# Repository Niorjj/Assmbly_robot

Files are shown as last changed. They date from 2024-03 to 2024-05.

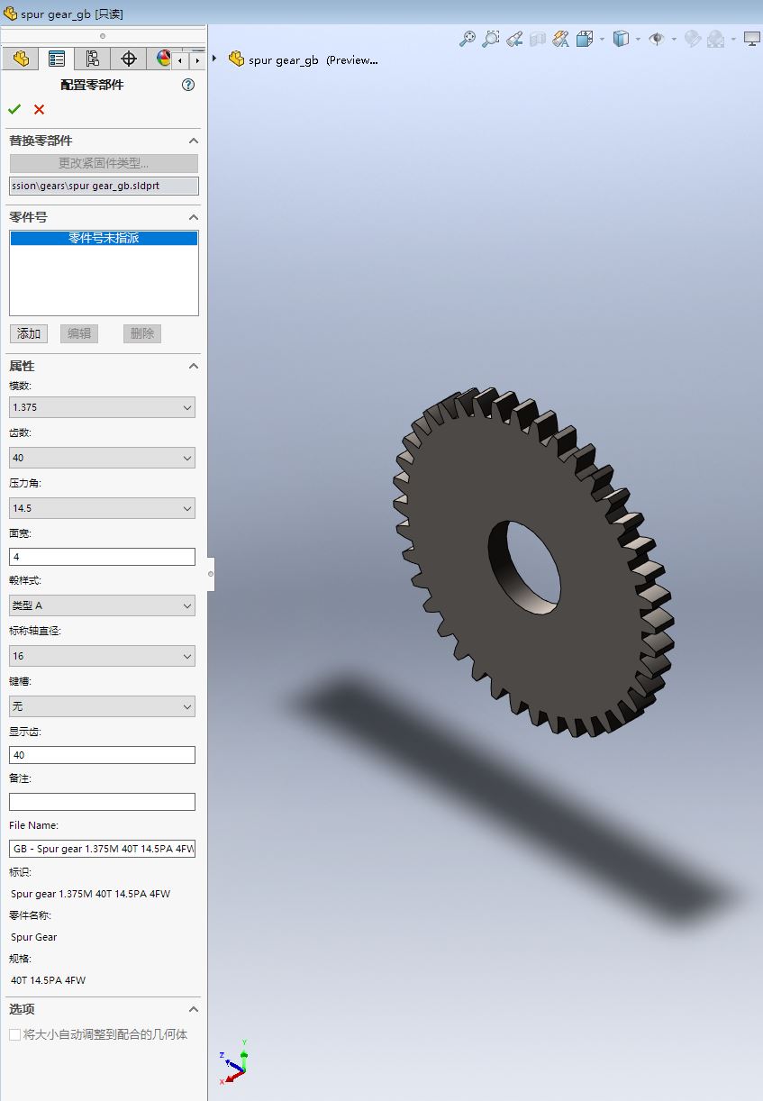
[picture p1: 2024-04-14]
Assembly_robot/hardware/MachineConstruction_project/solidworks/齿轮1_1.JPG

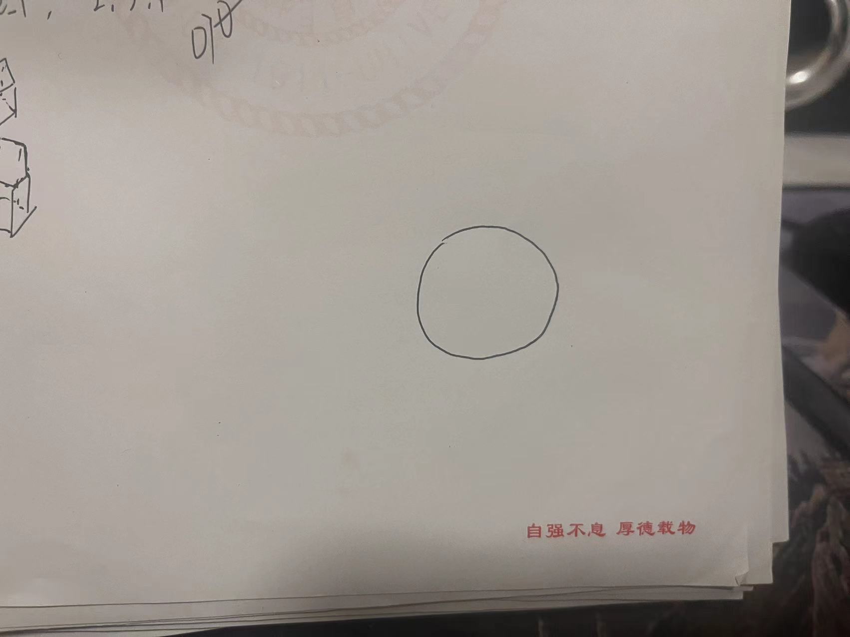
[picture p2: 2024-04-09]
Assembly_robot/software/Python_Code/test_circle.jpg

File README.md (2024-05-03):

<<<<<<< HEAD
## 项目简介

### 规则
=======
# Assembly_robot

### 项目简介

#### 规则
1. 传送带控制
**只需控制启动和停止，高电平启动，低电平停止**
2. 提供标准 220V 电源接口
**现场提供电源**
3. 待装配体旋转平台控制
**待装配体旋转平台接入PUL，DIR，EN三种信号**
4. 初始最大闭合区域
**450mm*450mm**
5. 布线层印有学校名称和2023，提供完整原理图和PCB图
6. 提供全套总装图和零件加工图

### 结构划分
=======

#### 项目流程图
1. 软件部分
   1. 树莓派相机标定
   2. 颜色与形状识别
   3. 串口通信将各电机转动角度发送到stm32上
   4. stm32驱动各电机转动
   5. 控制圆台和传送带
2. 外设资源分配
3. 原理图及pcb
4. 机械结构
5. 调试

#### 相机识别步骤
1. 相机标定
    相机标定的合格指标一共有四个，分别是*x轴方向*、*y轴方向*、*远近*以及*旋转角度*。
2. 相机和机械臂进行手眼标定
3. 读取摄像头信息
4. 识别出目标物体并得出位姿
5. 物体在相机中的二维坐标转化成相对于相机光心的三维坐标
6. 再转换成相对于机械臂底座的世界坐标
7. 计算机械臂末端执行器抓取物体时的位姿
8. 通过已知的目标位置和末端执行器的位姿信息来计算机械臂上每个电机应转动的角度
9.  根据有无障碍物、路径距离要求、时间要求规划出合适的路径
10. 驱动机械臂各个关节一步一步到达合适的位置
11. 末端执行器抓取物体
12. 投放到指定位置

#### 主要参数
1. **x**相机标定位置x坐标
2. **y**相机标定位置y坐标
3. **h**相机标定位置与相机距离
4. **r**相机标定识别物体旋转角度
5. **j1_Angle**大臂电机转动角度
6. **j2_Angle**小臂电机转动角度
7. **j3_Angle**底部电机转动角度
8. **j4_Angle**直线模组电机转动角度
9. **j5_Angle**机械爪夹取电机转动角度
10. **j6_Angle**舵机旋转角度
11. **PLANT_Angle**圆盘转动角度
12. **TRANS_State**传送带启停状态

#### 机械臂逆运动学求解
1. 确定目标位置
2. 求解各电机转动的角度python(Inverse_Kinematics)
3. Matlab Robotic System toolbox

#### 目前主要需要攻克的问题
1. 充分利用现有材料
2. 主控板用最小系统板，驱动板自制PCB
3. 直线模组的长度
4. 3D打印材料，受力情况
5. 模型尽量更改为用亚克力板，3D打印材料，铝型材组合的
6. 模型逆运动学，相机位置

后续正在补充ing....

<<<<<<< HEAD
### 
=======
####

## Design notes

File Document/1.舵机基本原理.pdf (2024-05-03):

# 舵机基本原理

最近几年国内机器人开始起步发展，很多高校、中小学都开始进行机器人技

术教学。小型的机器人、模块化的机器人、组件式的机器人是教学机器人的首选。

在这些机器人产品中，舵机是很关键，使用较多的部件。根据控制方式，舵机应

该称为微型伺服马达。早期在模型上使用最多，主要用于控制模型的舵面，所以

俗称舵机。舵机接受一个简单的控制指令就可以自动转动到一个比较精确的角

度，所以非常适合在关节型机器人产品使用。

## 1.舵机的结构

舵机简单的说就是集成了直流电机、电机控制器和减速器等，并封装在一个

便于安装的外壳里的伺服单元。能够利用简单的输入信号比较精确的转动给定角

度的电机系统。舵机安装了一个电位器（或其它角度传感器）检测输出轴转动角

度，控制板根据电位器的信息能比较精确的控制和保持输出轴的角度。这样的直

流电机控制方式叫闭环控制，所以舵机更准确的说是伺服马达，英文 servo。

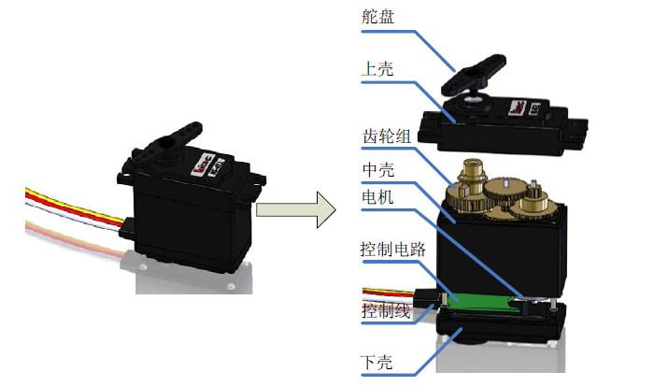
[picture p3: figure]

图 1 舵机的结构

舵机的主体结构如图 1 所示，主要有几个部分：外壳、减速齿轮组、电机、

电位器、控制电路。简单的工作原理是控制电路接收信号源的控制信号，并驱动

电机转动；齿轮组将电机的速度成大倍数缩小，并将电机的输出扭矩放大响应倍

数，然后输出；电位器和齿轮组的末级一起转动，测量舵机轴转动角度；电路板

检测并根据电位器判断舵机转动角度，然后控制舵机转动到目标角度或保持在目

标角度。

舵机的外壳一般是塑料的，特殊的舵机可能会有金属铝合金外壳。金属外壳

能够提供更好的散热，可以让舵机里面的电机运行在更高功率下，以提供更高的

扭矩输出。金属外壳也可以提供更牢固的固定位置。舵机的齿轮箱有塑料齿轮、

混合齿轮、金属齿轮的差别。塑料齿轮成本底，噪音小，但强度较低；金属齿轮

强度高，但成本高，在装配精度一般的情况下会有很大的噪音。小扭矩舵机、微

舵、扭矩大但功率密度小的舵机一般都用塑料齿轮，如 Futaba 3003，辉盛的 9g

微舵。金属齿轮一般用于功率密度较高的舵机上，比如辉盛的 MG995 舵机，在和

3003 一样体积的情况下却能提供 13KG 的扭矩。Hitec 甚至用钛合金作为齿轮材

料，其高强度能保证 3003 大小的舵机能提供 20 几公斤的扭矩。混合齿轮在金属

齿轮和塑料齿轮间做了折中，在电机输出减速箱扭矩不大的部位，用塑料齿轮。

## 2.舵机的规格和选型

2.1 舵机转速

转速由舵机无负载的情况下转过 60°角所需时间来衡量，常见舵机的速度

一般在 0.11s/60°-0.21s/60°之间。

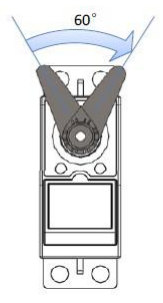
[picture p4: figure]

图 2 舵机的转速
2.2 舵机转矩

舵机扭矩的单位是 KG·CM，这是一个扭矩单位。可以理解为在舵盘上距舵

机轴中心水平距离 1CM 处，舵机能够带动的物体重量。

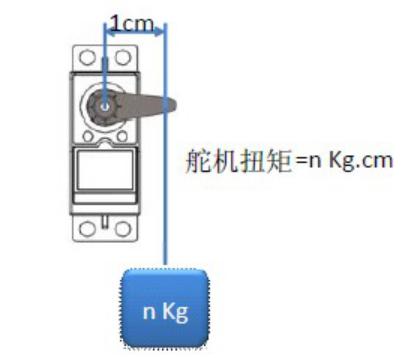
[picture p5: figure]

图 3 舵机的转矩

2.3 工作电压

厂商提供的速度、转矩数据和测试电压有关，在 4.8V 和 6V 两种测试电压下

这两个参数有比较大的差别。如 MG995 在 4.8V 时速度为 0.17 秒，在 6.0V 时

速度为 0.13 秒。舵机的工作电压对性能有重大的影响，舵机推荐的电压一般都

是 4.8V 或 6V。当然，有的舵机可以在 7V 以上工作，比如 12V 的舵机也不少。

具体更加较高的电压可以提高电机的速度和扭矩。选择舵机还需要看我们的控制

板所能提供的电压。

2.4 尺寸、重量和材质

舵机的功率（速度×转矩）和舵机的尺寸比值可以理解为该舵机的功率密度，

一般同样品牌的舵机，功率密度大的价格高。塑料齿轮的舵机在超出极限负荷的

条件下使用可能会崩齿，金属齿轮的舵机则可能会电机过热损毁或外壳变形。所

以材质的选择并没有绝对的倾向，关键是将舵机使用在设计规格之内。用户一般

都对金属制的物品比较信赖，齿轮箱期望选择全金属的，舵盘期望选择金属舵盘。

但需要注意的是，金属齿轮箱在长时间过载下也不会损毁，最后却是电机过热损

坏或外壳变形，而这样的损坏是致命的，不可修复的。塑料出轴的舵机如果使用

金属舵盘是很危险的，舵盘和舵机轴在相互扭转过程中，金属舵盘不会磨损，舵

机轴会在一段时间后变得光秃，导致舵机完全不能使用。综上，选择舵机需要在

计算自己所需扭矩和速度，并确定使用电压的条件下，选择有 150%左右甚至更

大扭矩富余的舵机。

## 3.舵机的工作原理

舵机是一个微型的伺服控制系统，具体的控制原理可以用下图表示：

工作原理是控制电路接收信号源的控制脉冲，并驱动电机转动；齿轮组将电

机的速度成大倍数缩小，并将电机的输出扭矩放大响应倍数，然后输出；电位器

和齿轮组的末级一起转动，测量舵机轴转动角度；电路板检测并根据电位器判断

舵机转动角度，然后控制舵机转动到目标角度或保持在目标角度。模拟舵机需要

一个外部控制器（遥控器的接收机或者单片机）产生脉宽调制信号来告诉舵机转

动角度，脉冲宽度是舵机控制器所需的编码信息。舵机的控制脉冲周期 20ms，

脉宽从 0.5ms-2.5ms，分别对应-90 度到+90 度的位置(对于 180°舵机)。如下图

所示：

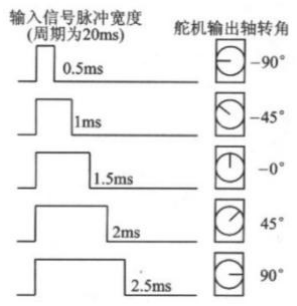
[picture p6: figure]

需要解释的是舵机原来主要用在飞机、汽车、船只模型上，作为方向舵的调

节和控制装置。所以，一般的转动范围是 45°、60°或者 90°，这时候脉冲宽

度一般只有 1ms-2ms 之间。而后舵机开始在机器人上得到大幅度的运用，转动的

角度也在根据机器人关节的需要增加到-90°至 90°之间,甚至还有-135°至

135°之间，脉冲宽度也随之有了变化。对与机器人控制而言，我们一般通过单

片机产生 PWM 信号控制舵机。

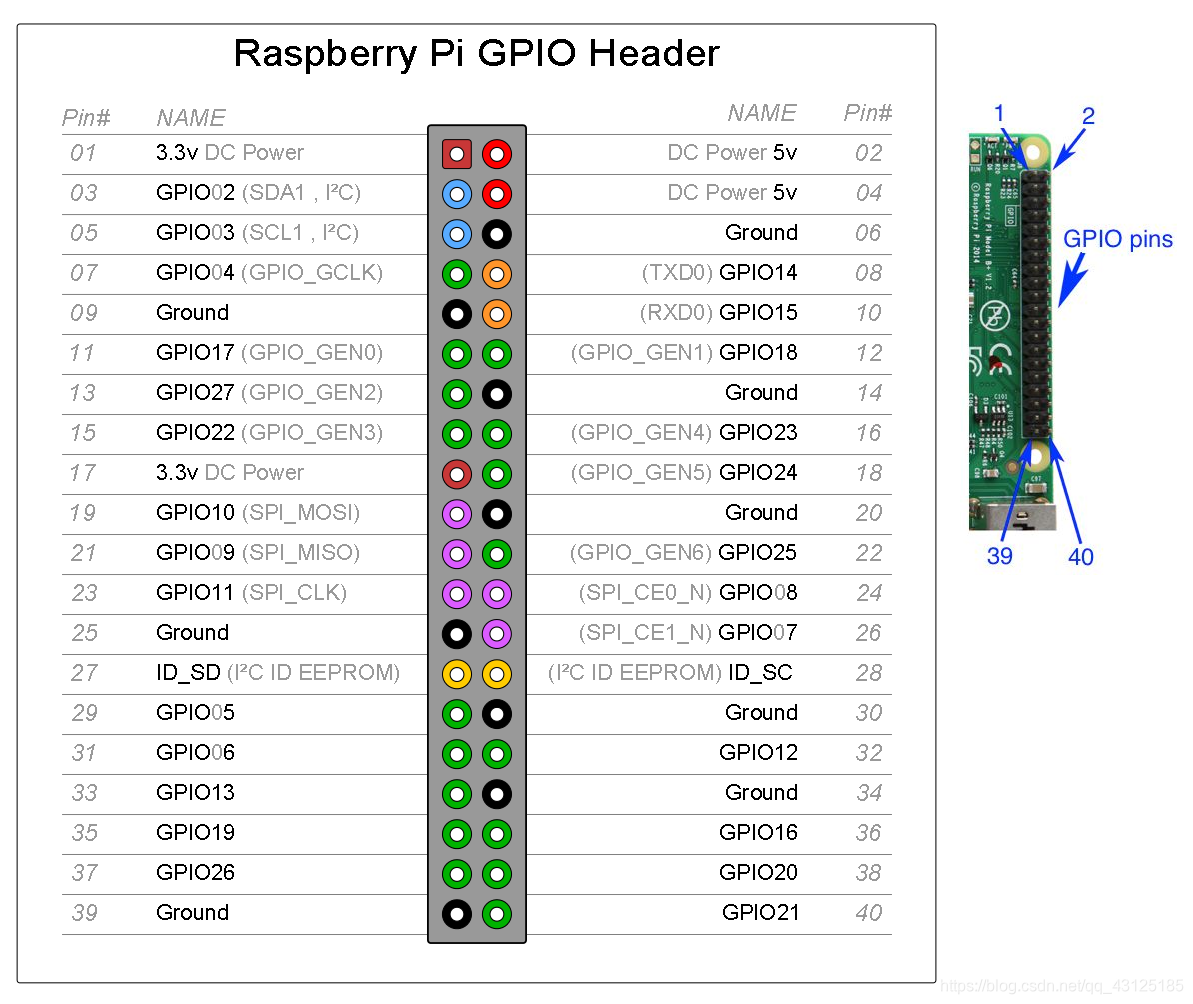
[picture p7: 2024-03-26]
Document/树莓派引脚图.jpg

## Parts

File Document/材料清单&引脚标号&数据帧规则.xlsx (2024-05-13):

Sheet: 材料表
结构分类 | 名称 | 型号 | 数量 | 单价 | 总价 | 备注
核心处理器 | 树莓派 |  | 1
 | 摄像头 |  | 1
控制器 | stm32f103RCT6最小系统板带屏幕 |  | 1 | 49.9 | 49.9
 | 驱动板 |  | 1 | 71.88 | 71.88 | PCB板20元，元器件51.88元
机械结构 | 步进电机 |  | 5 |  |  | 直线模组*1 底部旋转*1 大臂角和小臂角*2 机械爪抓取*1
 | 舵机 |  | 1
 | 联轴器
 | 直线丝杠装置 |  | 1
 | 外壳 |  |  |  |  | 3D打印制作，亚克力板，铝型材
 | 电源适配器 |  | 1 |  |  | 220V转12V
 | 传动齿轮
 | xh2.54-4p转母线 |  | 1 |  |  | 核心板串口连接树莓派
 | xh2.54-6p转公线 |  | 2 |  |  | 电机驱动板连接核心板

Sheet: 引脚
STM32F103RCT6 | 引脚名 | 功能 | 描述 | 树莓派 | 功能 | 功能 |  | 驱动板 |  | 电机 | 描述 | 传送带/装配圆盘
 | PA8 | TIM1_CH1 | 大臂舵机 |  |  |  | 接线端子 |  |  | SERVO1 | 大臂舵机
 | PA11 | TIM1_CH4 | 小臂舵机 |  |  |  |  |  |  | SERVO2 | 小臂舵机
 | PA1 | TIM2_CH2 | 底部旋转舵机 |  |  |  |  |  |  | SERVO3 | 底部旋转舵机
 | PA2 | TIM2_CH3 | 机械爪夹取舵机 |  |  |  |  |  |  | SERVO4 | 夹取舵机
 | PA3 | TIM2_CH4 | 机械爪旋转舵机 |  |  |  |  |  |  | SERVO5 | 旋转舵机
 | PC7 | TARANS | 传送带启停端 |  |  |  |  |  |  |  |  | D+ | 连接传送带启停端
 | PA1 | PLANT_DIR | 装配圆盘DIR |  |  |  |  |  |  |  |  | DIR
 | PC15 | PLANT_EN | 装配圆盘EN |  |  |  |  |  |  |  |  | EN
 | PB3 | MOTOR1_PUL | 底部步进电机PUL
 | PB4 | MOTOR1_DIR | 底部步进电机DIR
 | PB5 | MOTOR1_EN | 底部步进电机EN
 | PC10 | USART4_TX | 串口1输出 | GPIO15 | RX | 串口1输入
 | PC11 | USART4_RX | 串口1输入 | GPIO14 | TX | 串口1输出
 | PA13 | SWDIO | 调试数据段
 | PA14 | SWCLK | 调试时钟端
 | PD0 | HSE_IN
 | PD1 | HSE_OUT |  | 3.3V | 高电平点
 | VDD |  | 高电平点 | GND | 低电平点 |  |  | VCC | 连接5V
 | VSS |  | 低电平点 |  |  |  |  | GND
 | VBAT |  | 电池引脚 |  |  |  |  | VM | 连接12V
 | NRST |  | 复位引脚
 | PB2 | BOOT0 | 启动 |  |  |  |  | STBY | 连接5V
 |  | BOOT1

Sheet: 数据帧规则
数据位 | 数据 | 功能
Byte0 | 0xAA | 起始字节1
Byte1 | 0xBB | 起始字节2
Byte2 | J1_Angle | 大臂角度
Byte3 | J2_Angle | 小臂角度
Byte4 | J3_Angle | 底部旋转电机角度
Byte5 | J4_Angle | 底部平移电机角度
Byte6 | J5_ | 夹取舵机角度
Byte7 | J6_Angle | 旋转舵机角度
Byte8 | PLANT_Angle | 圆盘转动角度
Byte9 | TRANS_State | 传送带启停状态
Byte10 | 0xFF | 结束位
Bode_rate | 115200

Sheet: 角度对应规则
 | 500 | 800 | 1000 | 1450 | 1500 | 2000 | 2100
大臂舵机
小臂舵机
底部旋转舵机 |  | -90 |  | 0 |  |  | 90
机械爪夹取舵机 |  |  | 张开 |  | 张开 | 闭合
机械爪旋转舵机 | -45 |  | 0 |  | 45 | 90
 |  |  |  |  |  |  |  | s

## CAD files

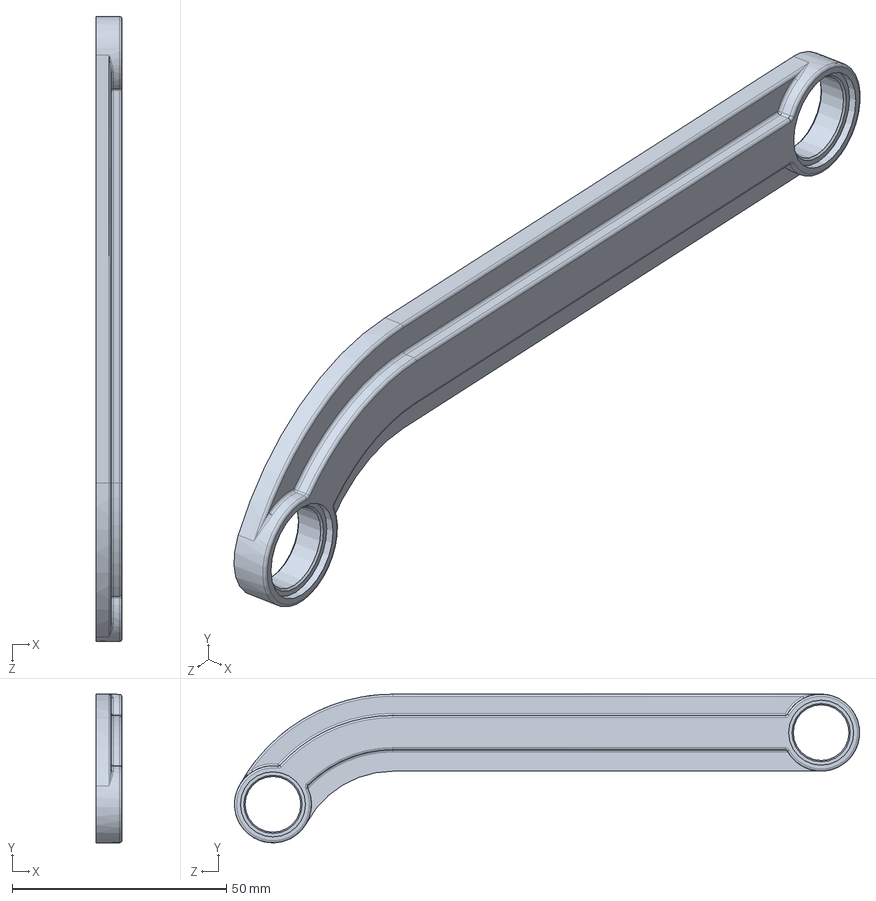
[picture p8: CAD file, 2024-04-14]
Assembly_robot/hardware/MachineConstruction_project/solidworks/零件6（2）.SLDPRT
6.00 x 34.7 x 145.9 mm

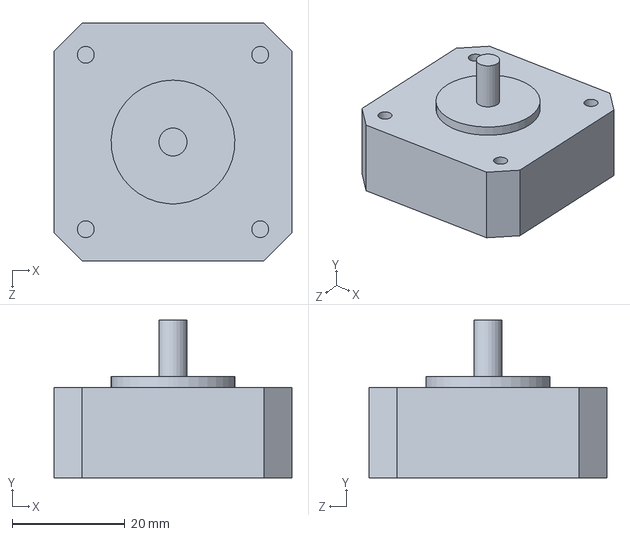
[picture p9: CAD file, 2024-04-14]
Assembly_robot/hardware/MachineConstruction_project/solidworks/电机2.SLDPRT
42.3 x 28.0 x 42.3 mm

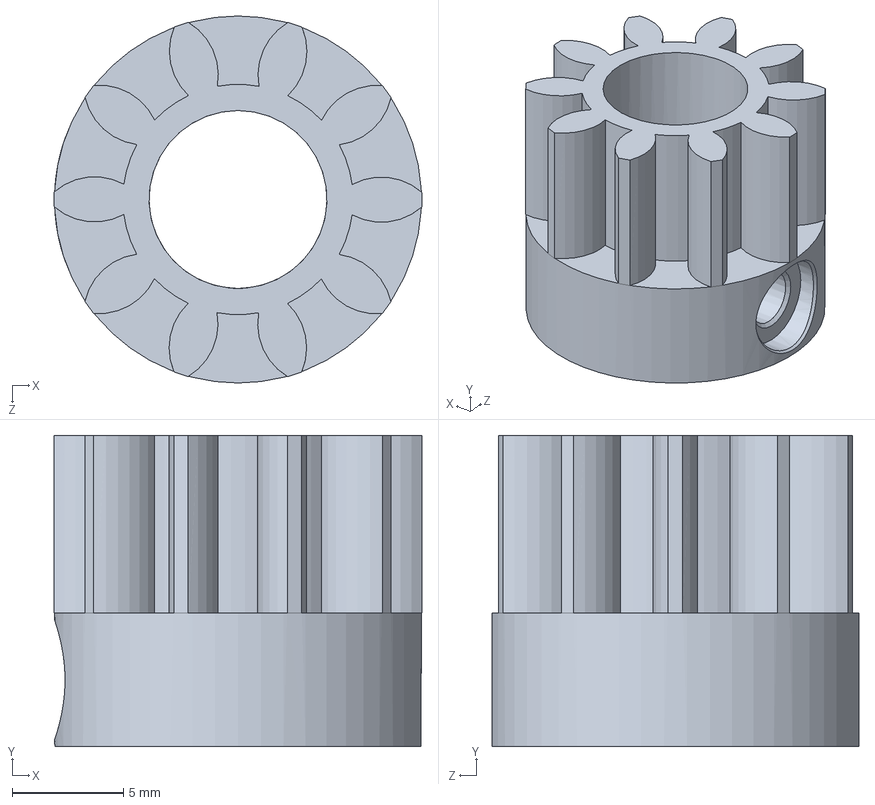
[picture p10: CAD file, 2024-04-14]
Assembly_robot/hardware/MachineConstruction_project/solidworks/齿轮3.1.SLDPRT
16.5 x 14.0 x 16.5 mm

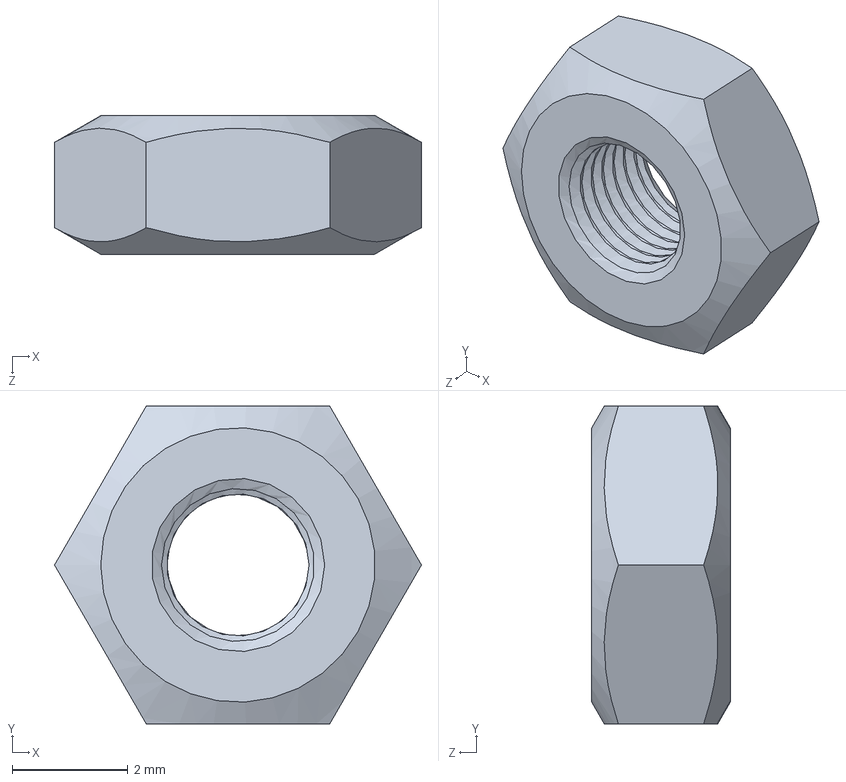
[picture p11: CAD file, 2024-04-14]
Assembly_robot/hardware/MachineConstruction_project/solidworks/M3-S_1.SLDPRT
6.35 x 5.50 x 2.40 mm

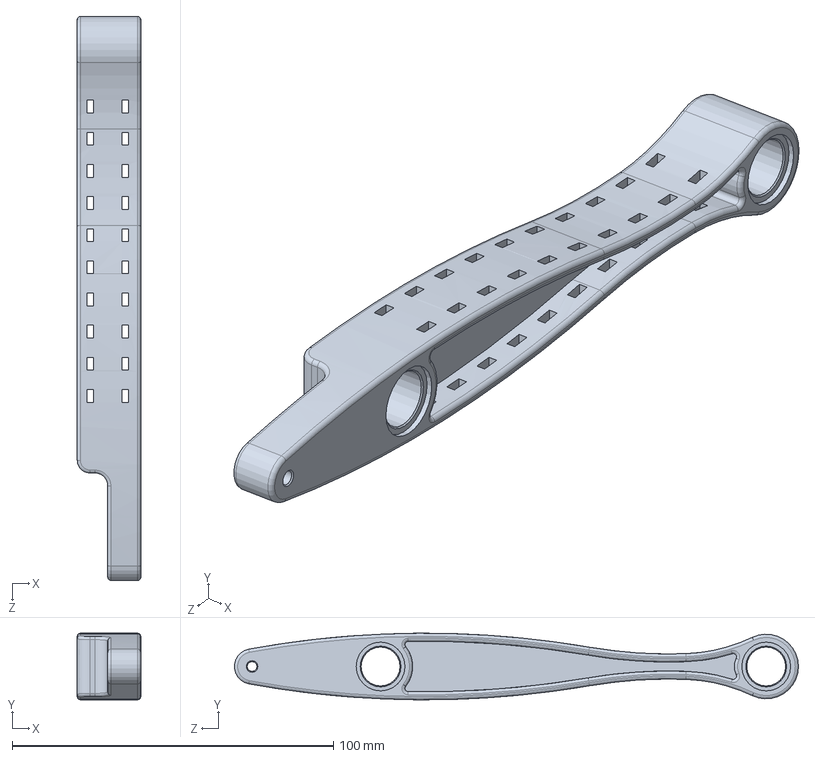
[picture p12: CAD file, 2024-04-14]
Assembly_robot/hardware/MachineConstruction_project/solidworks/零件4.SLDPRT
19.8 x 20.7 x 175.5 mm

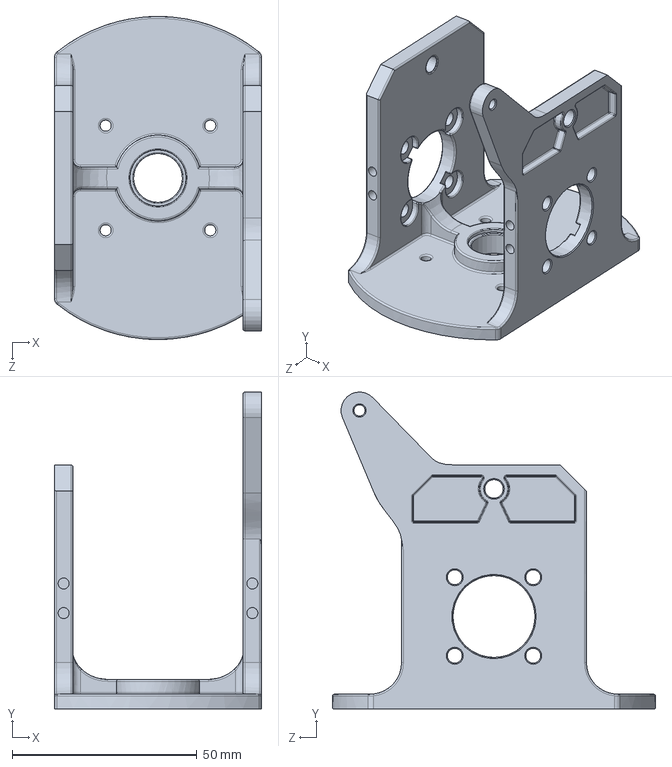
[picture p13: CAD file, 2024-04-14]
Assembly_robot/hardware/MachineConstruction_project/solidworks/零件1.SLDPRT
56.0 x 85.7 x 87.3 mm

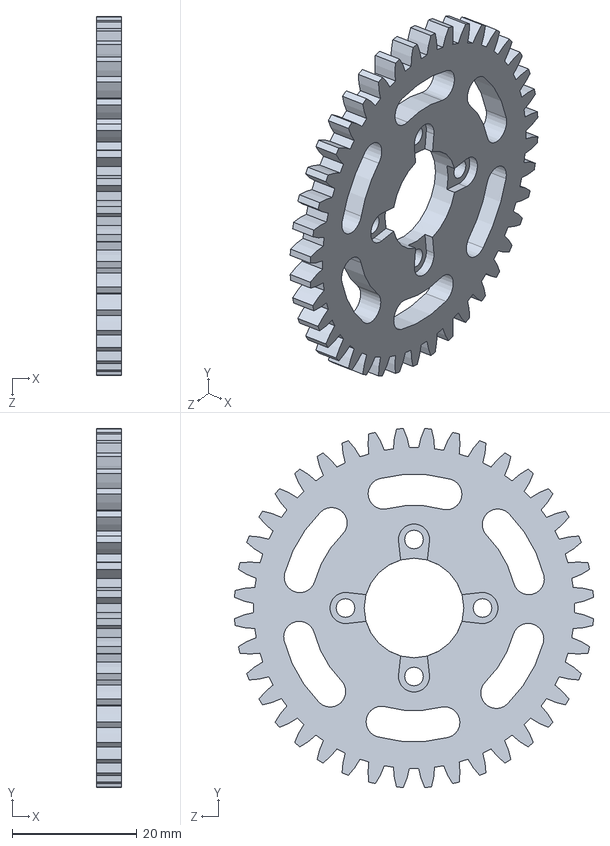
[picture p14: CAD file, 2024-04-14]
Assembly_robot/hardware/MachineConstruction_project/solidworks/齿轮1_1.SLDPRT
4.00 x 57.6 x 57.6 mm

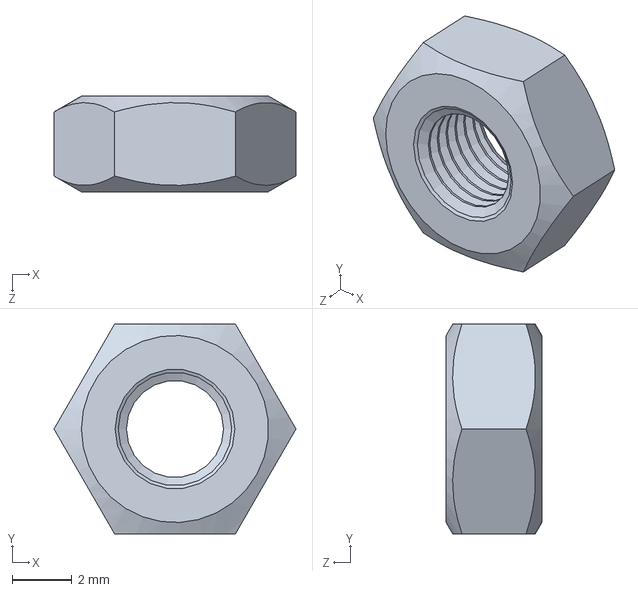
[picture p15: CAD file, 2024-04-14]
Assembly_robot/hardware/MachineConstruction_project/solidworks/M4-S.SLDPRT
8.08 x 7.00 x 3.20 mm

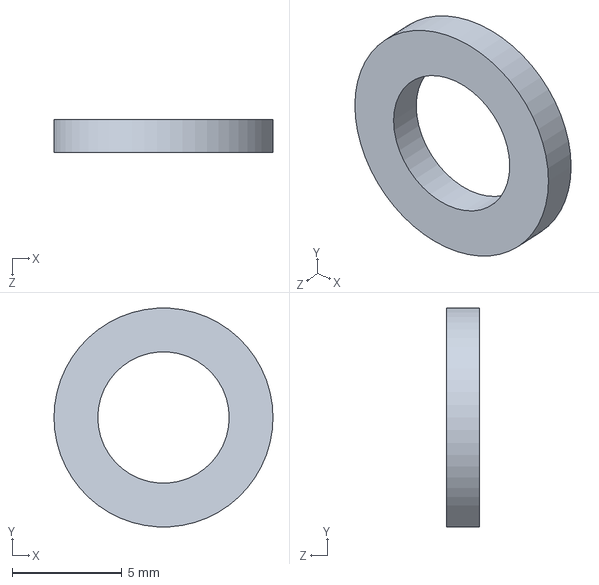
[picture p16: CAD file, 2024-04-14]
Assembly_robot/hardware/MachineConstruction_project/solidworks/垫片 1.5mm.SLDPRT
10.0 x 9.98 x 1.50 mm

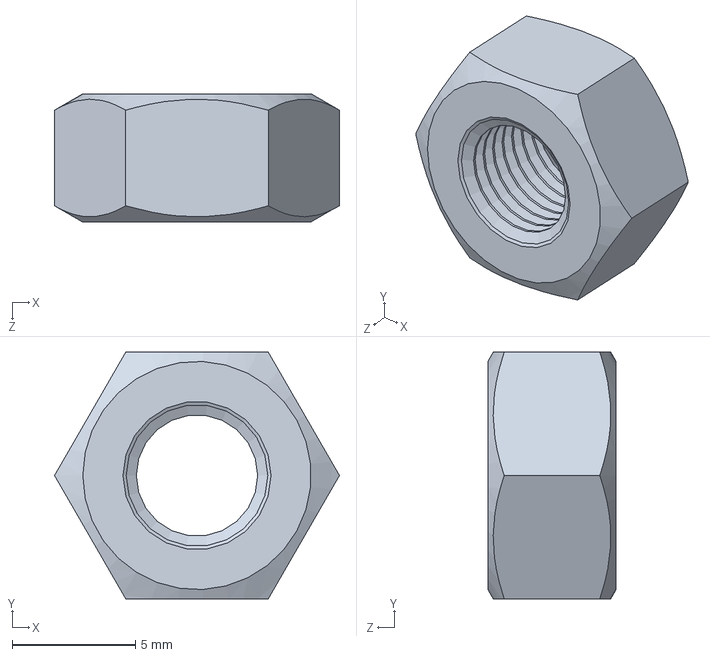
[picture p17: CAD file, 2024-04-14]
Assembly_robot/hardware/MachineConstruction_project/solidworks/M6-S_1.SLDPRT
11.5 x 10.0 x 5.20 mm

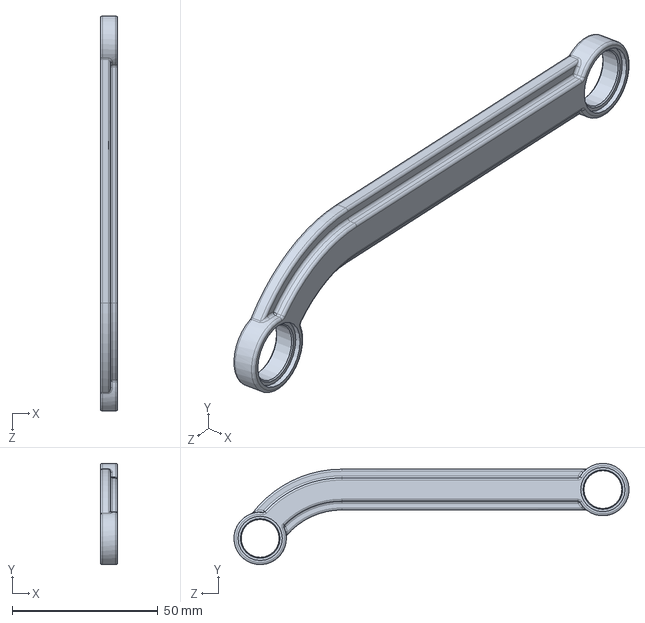
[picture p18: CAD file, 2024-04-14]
Assembly_robot/hardware/MachineConstruction_project/solidworks/零件6（1）.SLDPRT
6.00 x 34.7 x 135.4 mm

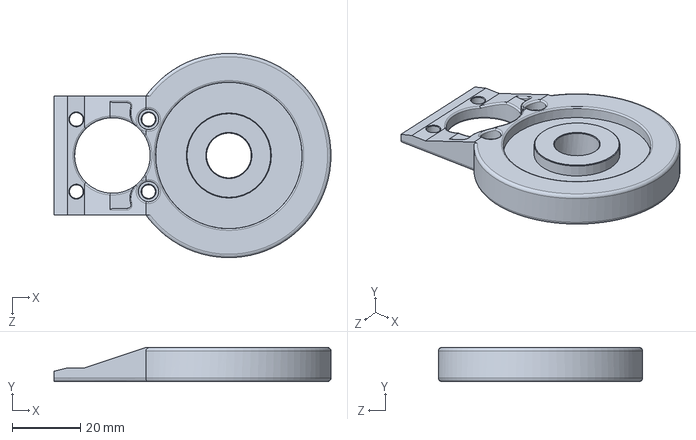
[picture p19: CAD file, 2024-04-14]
Assembly_robot/hardware/MachineConstruction_project/solidworks/零件5.SLDPRT
81.4 x 10.0 x 60.0 mm

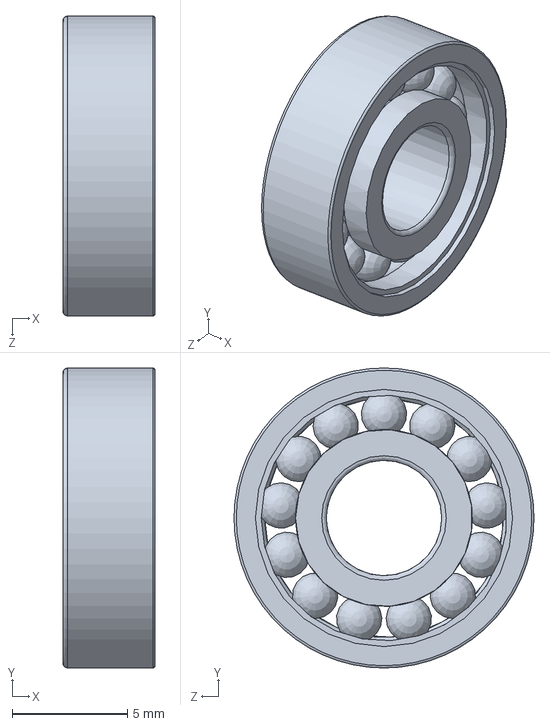
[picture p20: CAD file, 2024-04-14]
Assembly_robot/hardware/MachineConstruction_project/solidworks/轴承4x13x5 GB292-94.SLDPRT
4.00 x 13.0 x 13.0 mm

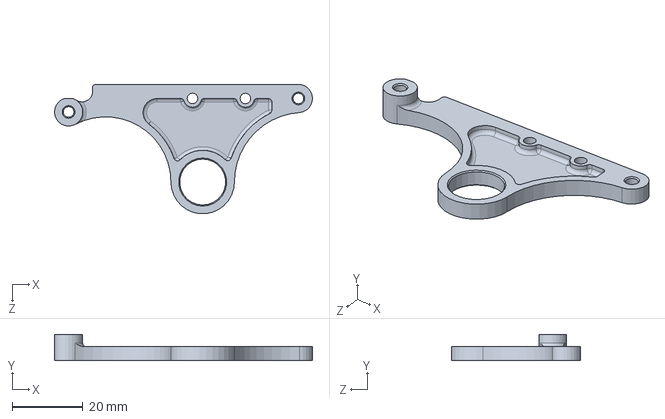
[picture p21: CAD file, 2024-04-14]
Assembly_robot/hardware/MachineConstruction_project/solidworks/零件9.SLDPRT
73.1 x 7.50 x 36.6 mm

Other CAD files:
Assembly_robot/hardware/MachineConstruction_project/solidworks/装配体1.SLDASM
Assembly_robot/hardware/MachineConstruction_project/solidworks/零件3.SLDPRT
Assembly_robot/hardware/MachineConstruction_project/solidworks/M3X30-S.SLDPRT
Assembly_robot/hardware/MachineConstruction_project/solidworks/M3X30-S_1.SLDPRT
Assembly_robot/hardware/MachineConstruction_project/solidworks/M3X40-S.SLDPRT
Assembly_robot/hardware/MachineConstruction_project/solidworks/M3X40-S_1.SLDPRT
Assembly_robot/hardware/MachineConstruction_project/solidworks/M3X6-S.SLDPRT
Assembly_robot/hardware/MachineConstruction_project/solidworks/M3X6-S_1.SLDPRT
Assembly_robot/hardware/MachineConstruction_project/solidworks/M3X8-S.SLDPRT
Assembly_robot/hardware/MachineConstruction_project/solidworks/M3X8-S_1.SLDPRT
Assembly_robot/hardware/MachineConstruction_project/solidworks/M4X12-S.SLDPRT
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

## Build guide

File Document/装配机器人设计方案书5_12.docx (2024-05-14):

装配机器人设计方案书

一、引言

- 项目背景：参加浙江省第八届大学生机器人竞赛，旨在通过实际操作提升学生的工程实践能力和创新思维。
- 设计目的：设计并制造一台能够高效、准确完成零件装配任务的机器人，以满足比赛规则要求并展示技术创新。

二、项目概述

- 功能需求：机器人需在规定时间内，将不同形状的零件从传送带上取下并准确装配到旋转台上的指定位置。
- 性能指标：装配精度±0.5mm，操作速度 1 零件/10 秒，系统响应时间<1 秒。
- 使用环境：比赛场地为 2000×3300 mm 的PVC 地板，环境光照稳定。

三、技术方案

- 总体设计：采用模块化设计，包括视觉识别模块、机械臂操作模块和控制系统模块。
- 硬件设计：
  - 传感器选择：使用视觉传感器（摄像头）进行零件形状， 位置以及装配孔形状识别。
  - 控制系统：采用STM32f103rct6 和树莓派作为主控制器，负责整体逻辑控制和信号调度。采用树莓派进行图像数据处理。
  - 执行机构：使用三轴机械臂，配备自适应机械爪以适应不同形状的零件。使用直线模组，实现机械臂整体稳定水平移动。
  - 用户界面：通过简宜OLED 显示屏显示当前状态和错误信息，操作者可通过开关进行基本的启停控制。

四、结构设计

- 机械结构：

** 机械臂：主要执行器有：步进电机 1，步进电机 2，舵机 1，舵机 2，舵机 3，舵机 4，舵机 5。编号依次为：motor1,motor2,servo1,servo2,servo3,servo4。

- 步进电机 1：控制直线模组螺杆，实现机械臂于平行传送带直线路径平移运动。
- 舵机 1：实现机械臂大臂的角度调节。
- 舵机 2：实现机械臂小臂的角度调节。
- 舵机 3：控制机械臂底部旋转自由度
- 舵机 4：控制机械爪张，合动作。
- 舵机 5：控制机械爪在机械爪与机械臂连接点处垂直平面

方向上的旋转动作。

机械臂由五个舵机控制。机械臂的底部有一个稳固的底座， 上有一个旋转转台，允许机械臂在水平面上旋转。主臂和 副臂通过铰链连结，使得机械臂可以在垂直或近似垂直方 向上移动。主臂提供基本的臂展和运动幅度。副臂支持主 臂工作并增强运动的精确性。

** 机械爪：可调节夹持器，能够根据零件大小和形状自动调整夹持力。由舵机 5 控制机械爪垂直平面旋转，舵机 4 控制机械爪张，合动作。

** 直线模组：由螺杆，套桶，装载平台，步进电机组成的简单运动模块。机械臂固定于装载平台上。由步进电机 1 驱动螺杆转动实现装载平台在搭载机械臂并在水平于传送带的一段路径上直线平移运动。

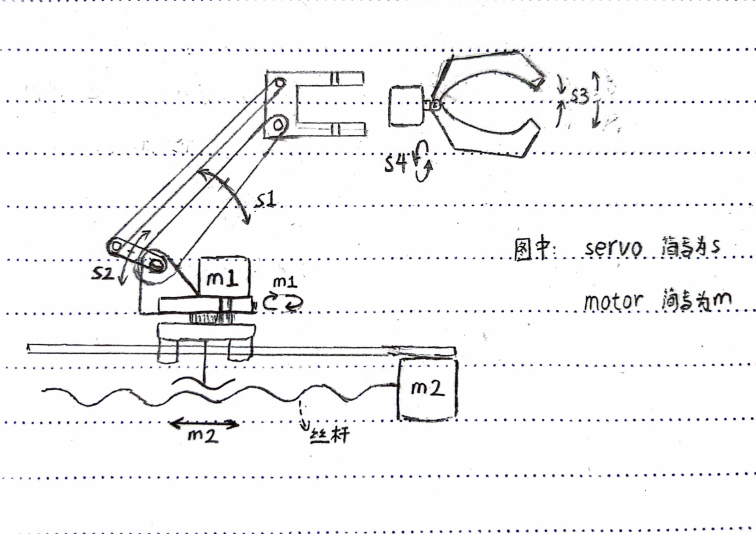
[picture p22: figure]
9272fee64799e10b50968b513c6e550

- 电路设计：

** 主控板：自制的 PCB 板，集成树莓派、电源模块和视觉传感器接口。

** 驱动板：采用 DM542C作为电机驱动器控制步进电机

** 电源系统：使用电源适配器将 220V 交流电转为 12V 直

流电。再通过自制电压转换模块为各部件提供适当的电压。

五、工作原理

- 操作流程：机器人启动后，相机首先识别传送带上的零件形状和位置，信息传递给树莓派，树莓派计算出最优取件和装配路径并将运动数据传给 STM32，由STM32 指挥机械臂执行操作。

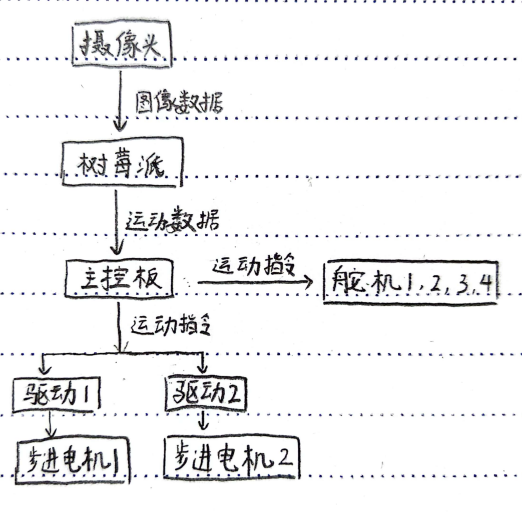
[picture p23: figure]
ee1da2044ea720df489a8835edf82c8

- 数据传输：STM32的PA8和PA9排母用杜邦线和树莓派连接，

数据传输采用元素为十六进制的数组。帧头为 0x0d(Carriage Return);帧尾为 0x0a(Line Feed)。排除帧头和帧尾，数组内元素即为各执行器运动数据，依次是：步进电机1，步进电机2，舵机1，舵机2，舵机3，舵机4。

- 机器人运动数据处理：

技术路线：

1.运动学模型建立： 使用Denavit-Hartenberg方法来定义机器人各关节和连杆的参数，建立数学模型。

具体计算过程如下：

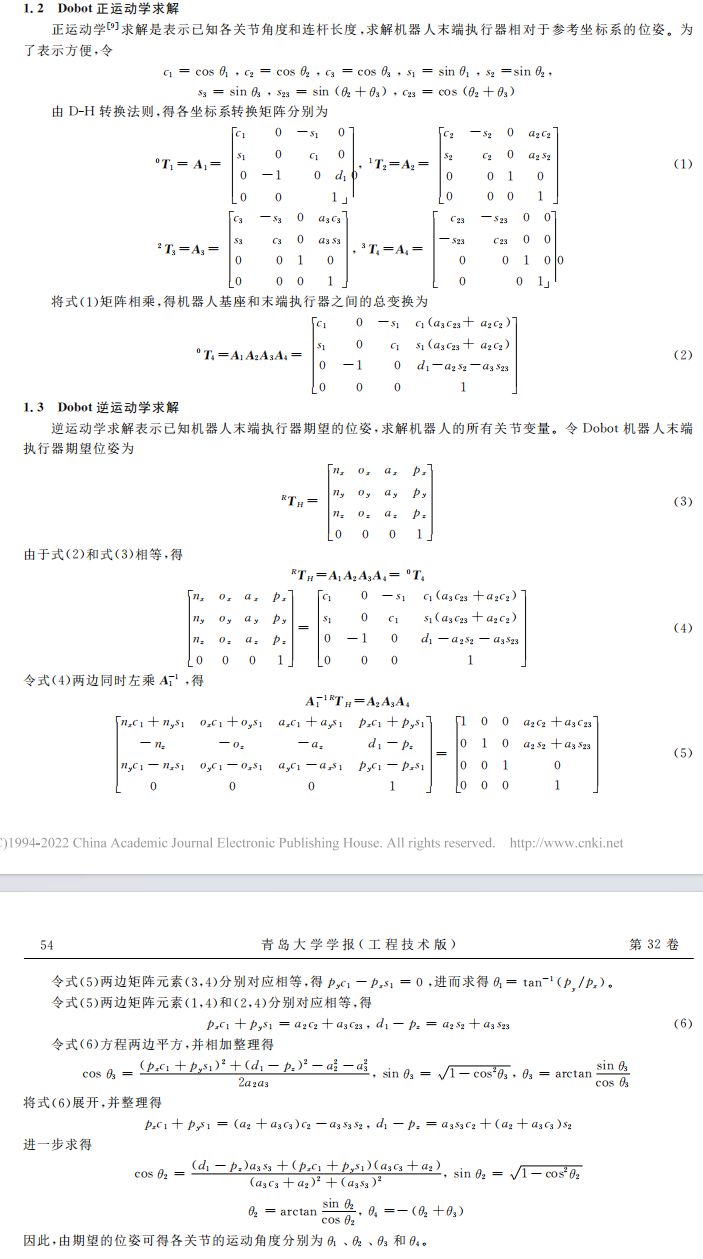
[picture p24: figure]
17330925148a53305fc21809c9e7256

2.轨迹规划： 采用关节空间轨迹规划中五次多项式插值法来设计机器人从起始点到终点的运动轨迹，确保运动过程中速度和加速度的连续性和平滑性。

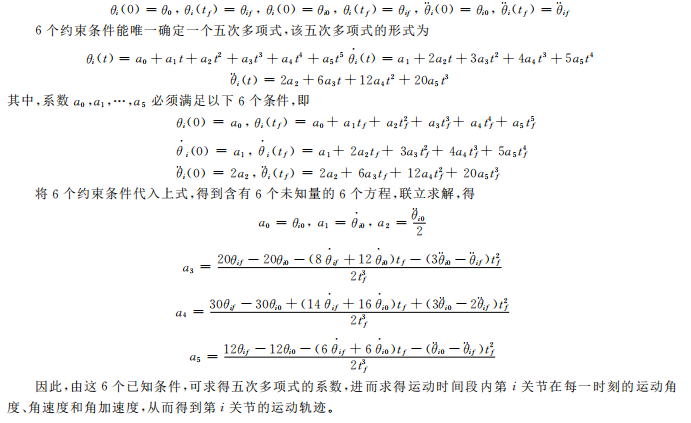
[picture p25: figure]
85b53d7fa4e1bf50e1289b9c029427e

3.仿真验证： 利用Matlab Robotics Toolbox进行正逆运动学计算和轨迹规划的仿真，检验设计的可行性和效果。

- 机器人视觉图像处理：

六、系统集成与测试

- 集成方法：首先单独测试各模块功能，然后进行系统级集

成测试，最后进行全系统的性能测试。

- 测试计划：包括静态功能测试、动态性能测试和实际装配测试，确保机器人在各种条件下都能稳定工作。

七、结论

- 项目总结：本设计方案充分考虑了比赛规则和实际操作需求，通过创新的设计和精确的控制，能够有效完成比赛任务。

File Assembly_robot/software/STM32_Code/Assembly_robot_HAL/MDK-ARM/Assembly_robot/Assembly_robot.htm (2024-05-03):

# Static Call Graph for image Assembly_robot\Assembly_robot.axf

#<CALLGRAPH># ARM Linker, 5060528: Last Updated: Thu Apr 18 20:51:47 2024

### Maximum Stack Usage = 136 bytes + Unknown(Functions without stacksize, Cycles, Untraceable Function Pointers)

### Call chain for Maximum Stack Depth:

__rt_entry_main ⇒ main ⇒ MX_TIM3_Init ⇒ HAL_TIM_MspPostInit ⇒ HAL_GPIO_Init

### Functions with no stack information

- __user_initial_stackheap

### Mutually Recursive functions

- ADC1_2_IRQHandler ⇒ ADC1_2_IRQHandler
- BusFault_Handler ⇒ BusFault_Handler
- HardFault_Handler ⇒ HardFault_Handler
- MemManage_Handler ⇒ MemManage_Handler
- NMI_Handler ⇒ NMI_Handler
- UART_EndRxTransfer ⇒ UART_EndRxTransfer
- UsageFault_Handler ⇒ UsageFault_Handler

### Function Pointers

- ADC1_2_IRQHandler from startup_stm32f103xe.o(.text) referenced from startup_stm32f103xe.o(RESET)
- ADC3_IRQHandler from startup_stm32f103xe.o(.text) referenced from startup_stm32f103xe.o(RESET)
- BusFault_Handler from stm32f1xx_it.o(i.BusFault_Handler) referenced from startup_stm32f103xe.o(RESET)
- CAN1_RX1_IRQHandler from startup_stm32f103xe.o(.text) referenced from startup_stm32f103xe.o(RESET)
- CAN1_SCE_IRQHandler from startup_stm32f103xe.o(.text) referenced from startup_stm32f103xe.o(RESET)
- DMA1_Channel1_IRQHandler from startup_stm32f103xe.o(.text) referenced from startup_stm32f103xe.o(RESET)
- DMA1_Channel2_IRQHandler from startup_stm32f103xe.o(.text) referenced from startup_stm32f103xe.o(RESET)
- DMA1_Channel3_IRQHandler from startup_stm32f103xe.o(.text) referenced from startup_stm32f103xe.o(RESET)
- DMA1_Channel4_IRQHandler from startup_stm32f103xe.o(.text) referenced from startup_stm32f103xe.o(RESET)
- DMA1_Channel5_IRQHandler from startup_stm32f103xe.o(.text) referenced from startup_stm32f103xe.o(RESET)
- DMA1_Channel6_IRQHandler from startup_stm32f103xe.o(.text) referenced from startup_stm32f103xe.o(RESET)
- DMA1_Channel7_IRQHandler from startup_stm32f103xe.o(.text) referenced from startup_stm32f103xe.o(RESET)
- DMA2_Channel1_IRQHandler from startup_stm32f103xe.o(.text) referenced from startup_stm32f103xe.o(RESET)
- DMA2_Channel2_IRQHandler from startup_stm32f103xe.o(.text) referenced from startup_stm32f103xe.o(RESET)
- DMA2_Channel3_IRQHandler from startup_stm32f103xe.o(.text) referenced from startup_stm32f103xe.o(RESET)
- DMA2_Channel4_5_IRQHandler from startup_stm32f103xe.o(.text) referenced from startup_stm32f103xe.o(RESET)
- DebugMon_Handler from stm32f1xx_it.o(i.DebugMon_Handler) referenced from startup_stm32f103xe.o(RESET)
- EXTI0_IRQHandler from startup_stm32f103xe.o(.text) referenced from startup_stm32f103xe.o(RESET)
- EXTI15_10_IRQHandler from startup_stm32f103xe.o(.text) referenced from startup_stm32f103xe.o(RESET)
- EXTI1_IRQHandler from startup_stm32f103xe.o(.text) referenced from startup_stm32f103xe.o(RESET)
- EXTI2_IRQHandler from startup_stm32f103xe.o(.text) referenced from startup_stm32f103xe.o(RESET)
- EXTI3_IRQHandler from startup_stm32f103xe.o(.text) referenced from startup_stm32f103xe.o(RESET)
- EXTI4_IRQHandler from startup_stm32f103xe.o(.text) referenced from startup_stm32f103xe.o(RESET)
- EXTI9_5_IRQHandler from startup_stm32f103xe.o(.text) referenced from startup_stm32f103xe.o(RESET)
- FLASH_IRQHandler from startup_stm32f103xe.o(.text) referenced from startup_stm32f103xe.o(RESET)
- FSMC_IRQHandler from startup_stm32f103xe.o(.text) referenced from startup_stm32f103xe.o(RESET)
- HardFault_Handler from stm32f1xx_it.o(i.HardFault_Handler) referenced from startup_stm32f103xe.o(RESET)
- I2C1_ER_IRQHandler from startup_stm32f103xe.o(.text) referenced from startup_stm32f103xe.o(RESET)
- I2C1_EV_IRQHandler from startup_stm32f103xe.o(.text) referenced from startup_stm32f103xe.o(RESET)
- I2C2_ER_IRQHandler from startup_stm32f103xe.o(.text) referenced from startup_stm32f103xe.o(RESET)
- I2C2_EV_IRQHandler from startup_stm32f103xe.o(.text) referenced from startup_stm32f103xe.o(RESET)
- MemManage_Handler from stm32f1xx_it.o(i.MemManage_Handler) referenced from startup_stm32f103xe.o(RESET)
- NMI_Handler from stm32f1xx_it.o(i.NMI_Handler) referenced from startup_stm32f103xe.o(RESET)
- PVD_IRQHandler from startup_stm32f103xe.o(.text) referenced from startup_stm32f103xe.o(RESET)
- PendSV_Handler from stm32f1xx_it.o(i.PendSV_Handler) referenced from startup_stm32f103xe.o(RESET)
- RCC_IRQHandler from startup_stm32f103xe.o(.text) referenced from startup_stm32f103xe.o(RESET)
- RTC_Alarm_IRQHandler from startup_stm32f103xe.o(.text) referenced from startup_stm32f103xe.o(RESET)
- RTC_IRQHandler from startup_stm32f103xe.o(.text) referenced from startup_stm32f103xe.o(RESET)
- Reset_Handler from startup_stm32f103xe.o(.text) referenced from startup_stm32f103xe.o(RESET)
- SDIO_IRQHandler from startup_stm32f103xe.o(.text) referenced from startup_stm32f103xe.o(RESET)
- SPI1_IRQHandler from startup_stm32f103xe.o(.text) referenced from startup_stm32f103xe.o(RESET)
- SPI2_IRQHandler from startup_stm32f103xe.o(.text) referenced from startup_stm32f103xe.o(RESET)
- SPI3_IRQHandler from startup_stm32f103xe.o(.text) referenced from startup_stm32f103xe.o(RESET)
- SVC_Handler from stm32f1xx_it.o(i.SVC_Handler) referenced from startup_stm32f103xe.o(RESET)
- SysTick_Handler from stm32f1xx_it.o(i.SysTick_Handler) referenced from startup_stm32f103xe.o(RESET)
- SystemInit from system_stm32f1xx.o(i.SystemInit) referenced from startup_stm32f103xe.o(.text)
- TAMPER_IRQHandler from startup_stm32f103xe.o(.text) referenced from startup_stm32f103xe.o(RESET)
- TIM1_BRK_IRQHandler from startup_stm32f103xe.o(.text) referenced from startup_stm32f103xe.o(RESET)
- TIM1_CC_IRQHandler from startup_stm32f103xe.o(.text) referenced from startup_stm32f103xe.o(RESET)
- TIM1_TRG_COM_IRQHandler from startup_stm32f103xe.o(.text) referenced from startup_stm32f103xe.o(RESET)
- TIM1_UP_IRQHandler from startup_stm32f103xe.o(.text) referenced from startup_stm32f103xe.o(RESET)
- TIM2_IRQHandler from startup_stm32f103xe.o(.text) referenced from startup_stm32f103xe.o(RESET)
- TIM3_IRQHandler from startup_stm32f103xe.o(.text) referenced from startup_stm32f103xe.o(RESET)
- TIM4_IRQHandler from startup_stm32f103xe.o(.text) referenced from startup_stm32f103xe.o(RESET)
- TIM5_IRQHandler from startup_stm32f103xe.o(.text) referenced from startup_stm32f103xe.o(RESET)
- TIM6_IRQHandler from startup_stm32f103xe.o(.text) referenced from startup_stm32f103xe.o(RESET)
- TIM7_IRQHandler from startup_stm32f103xe.o(.text) referenced from startup_stm32f103xe.o(RESET)
- TIM8_BRK_IRQHandler from startup_stm32f103xe.o(.text) referenced from startup_stm32f103xe.o(RESET)
- TIM8_CC_IRQHandler from startup_stm32f103xe.o(.text) referenced from startup_stm32f103xe.o(RESET)
- TIM8_TRG_COM_IRQHandler from startup_stm32f103xe.o(.text) referenced from startup_stm32f103xe.o(RESET)
- TIM8_UP_IRQHandler from startup_stm32f103xe.o(.text) referenced from startup_stm32f103xe.o(RESET)
- UART4_IRQHandler from startup_stm32f103xe.o(.text) referenced from startup_stm32f103xe.o(RESET)
- UART5_IRQHandler from startup_stm32f103xe.o(.text) referenced from startup_stm32f103xe.o(RESET)
- UART_DMAAbortOnError from stm32f1xx_hal_uart.o(i.UART_DMAAbortOnError) referenced from stm32f1xx_hal_uart.o(i.HAL_UART_IRQHandler)
- USART1_IRQHandler from stm32f1xx_it.o(i.USART1_IRQHandler) referenced from startup_stm32f103xe.o(RESET)
- USART2_IRQHandler from startup_stm32f103xe.o(.text) referenced from startup_stm32f103xe.o(RESET)
- USART3_IRQHandler from startup_stm32f103xe.o(.text) referenced from startup_stm32f103xe.o(RESET)
- USBWakeUp_IRQHandler from startup_stm32f103xe.o(.text) referenced from startup_stm32f103xe.o(RESET)
- USB_HP_CAN1_TX_IRQHandler from startup_stm32f103xe.o(.text) referenced from startup_stm32f103xe.o(RESET)
- USB_LP_CAN1_RX0_IRQHandler from startup_stm32f103xe.o(.text) referenced from startup_stm32f103xe.o(RESET)
- UsageFault_Handler from stm32f1xx_it.o(i.UsageFault_Handler) referenced from startup_stm32f103xe.o(RESET)
- WWDG_IRQHandler from startup_stm32f103xe.o(.text) referenced from startup_stm32f103xe.o(RESET)
- __main from __main.o(!!!main) referenced from startup_stm32f103xe.o(.text)

### Global Symbols

__main (Thumb, 8 bytes, Stack size 0 bytes, __main.o(!!!main))

[Calls]

- >> __rt_entry
- >> __scatterload

__scatterload (Thumb, 0 bytes, Stack size unknown bytes, __scatter.o(!!!scatter))

[Called By]

- >> __main

__scatterload_rt2 (Thumb, 44 bytes, Stack size unknown bytes, __scatter.o(!!!scatter), UNUSED)

[Calls]

- >> __rt_entry

__scatterload_rt2_thumb_only (Thumb, 0 bytes, Stack size unknown bytes, __scatter.o(!!!scatter), UNUSED)

__scatterload_null (Thumb, 0 bytes, Stack size unknown bytes, __scatter.o(!!!scatter), UNUSED)

__scatterload_copy (Thumb, 26 bytes, Stack size unknown bytes, __scatter_copy.o(!!handler_copy), UNUSED)

[Calls]

- >> __scatterload_copy

[Called By]

- >> __scatterload_copy

__scatterload_zeroinit (Thumb, 28 bytes, Stack size unknown bytes, __scatter_zi.o(!!handler_zi), UNUSED)

__rt_lib_init (Thumb, 0 bytes, Stack size unknown bytes, libinit.o(.ARM.Collect$$libinit$$00000000))

[Called By]

- >> __rt_entry_li

__rt_lib_init_alloca_1 (Thumb, 0 bytes, Stack size unknown bytes, libinit2.o(.ARM.Collect$$libinit$$0000002E))

__rt_lib_init_argv_1 (Thumb, 0 bytes, Stack size unknown bytes, libinit2.o(.ARM.Collect$$libinit$$0000002C))

__rt_lib_init_atexit_1 (Thumb, 0 bytes, Stack size unknown bytes, libinit2.o(.ARM.Collect$$libinit$$0000001B))

__rt_lib_init_clock_1 (Thumb, 0 bytes, Stack size unknown bytes, libinit2.o(.ARM.Collect$$libinit$$00000021))

__rt_lib_init_cpp_1 (Thumb, 0 bytes, Stack size unknown bytes, libinit2.o(.ARM.Collect$$libinit$$00000032))

__rt_lib_init_exceptions_1 (Thumb, 0 bytes, Stack size unknown bytes, libinit2.o(.ARM.Collect$$libinit$$00000030))

__rt_lib_init_fp_1 (Thumb, 0 bytes, Stack size unknown bytes, libinit2.o(.ARM.Collect$$libinit$$00000002))

__rt_lib_init_fp_trap_1 (Thumb, 0 bytes, Stack size unknown bytes, libinit2.o(.ARM.Collect$$libinit$$0000001F))

__rt_lib_init_getenv_1 (Thumb, 0 bytes, Stack size unknown bytes, libinit2.o(.ARM.Collect$$libinit$$00000023))

__rt_lib_init_heap_1 (Thumb, 0 bytes, Stack size unknown bytes, libinit2.o(.ARM.Collect$$libinit$$0000000A))

__rt_lib_init_lc_collate_1 (Thumb, 0 bytes, Stack size unknown bytes, libinit2.o(.ARM.Collect$$libinit$$00000011))

__rt_lib_init_lc_ctype_1 (Thumb, 0 bytes, Stack size unknown bytes, libinit2.o(.ARM.Collect$$libinit$$00000013))

__rt_lib_init_lc_monetary_1 (Thumb, 0 bytes, Stack size unknown bytes, libinit2.o(.ARM.Collect$$libinit$$00000015))

__rt_lib_init_lc_numeric_1 (Thumb, 0 bytes, Stack size unknown bytes, libinit2.o(.ARM.Collect$$libinit$$00000017))

__rt_lib_init_lc_time_1 (Thumb, 0 bytes, Stack size unknown bytes, libinit2.o(.ARM.Collect$$libinit$$00000019))

__rt_lib_init_preinit_1 (Thumb, 0 bytes, Stack size unknown bytes, libinit2.o(.ARM.Collect$$libinit$$00000004))

__rt_lib_init_rand_1 (Thumb, 0 bytes, Stack size unknown bytes, libinit2.o(.ARM.Collect$$libinit$$0000000E))

__rt_lib_init_return (Thumb, 0 bytes, Stack size unknown bytes, libinit2.o(.ARM.Collect$$libinit$$00000033))

__rt_lib_init_signal_1 (Thumb, 0 bytes, Stack size unknown bytes, libinit2.o(.ARM.Collect$$libinit$$0000001D))

__rt_lib_init_stdio_1 (Thumb, 0 bytes, Stack size unknown bytes, libinit2.o(.ARM.Collect$$libinit$$00000025))

__rt_lib_init_user_alloc_1 (Thumb, 0 bytes, Stack size unknown bytes, libinit2.o(.ARM.Collect$$libinit$$0000000C))

__rt_lib_shutdown (Thumb, 0 bytes, Stack size unknown bytes, libshutdown.o(.ARM.Collect$$libshutdown$$00000000))

[Called By]

- >> __rt_exit_ls

__rt_lib_shutdown_cpp_1 (Thumb, 0 bytes, Stack size unknown bytes, libshutdown2.o(.ARM.Collect$$libshutdown$$00000002))

__rt_lib_shutdown_fp_trap_1 (Thumb, 0 bytes, Stack size unknown bytes, libshutdown2.o(.ARM.Collect$$libshutdown$$00000007))

__rt_lib_shutdown_heap_1 (Thumb, 0 bytes, Stack size unknown bytes, libshutdown2.o(.ARM.Collect$$libshutdown$$0000000F))

__rt_lib_shutdown_return (Thumb, 0 bytes, Stack size unknown bytes, libshutdown2.o(.ARM.Collect$$libshutdown$$00000010))

__rt_lib_shutdown_signal_1 (Thumb, 0 bytes, Stack size unknown bytes, libshutdown2.o(.ARM.Collect$$libshutdown$$0000000A))

__rt_lib_shutdown_stdio_1 (Thumb, 0 bytes, Stack size unknown bytes, libshutdown2.o(.ARM.Collect$$libshutdown$$00000004))

__rt_lib_shutdown_user_alloc_1 (Thumb, 0 bytes, Stack size unknown bytes, libshutdown2.o(.ARM.Collect$$libshutdown$$0000000C))

__rt_entry (Thumb, 0 bytes, Stack size unknown bytes, __rtentry.o(.ARM.Collect$$rtentry$$00000000))

[Called By]

- >> __main
- >> __scatterload_rt2

__rt_entry_presh_1 (Thumb, 0 bytes, Stack size unknown bytes, __rtentry2.o(.ARM.Collect$$rtentry$$00000002))

__rt_entry_sh (Thumb, 0 bytes, Stack size unknown bytes, __rtentry4.o(.ARM.Collect$$rtentry$$00000004))

[Stack]

- Max Depth = 8 + Unknown Stack Size
- Call Chain = __rt_entry_sh ⇒ __user_setup_stackheap

[Calls]

- >> __user_setup_stackheap

__rt_entry_li (Thumb, 0 bytes, Stack size unknown bytes, __rtentry2.o(.ARM.Collect$$rtentry$$0000000A))

[Calls]

- >> __rt_lib_init

__rt_entry_postsh_1 (Thumb, 0 bytes, Stack size unknown bytes, __rtentry2.o(.ARM.Collect$$rtentry$$00000009))

__rt_entry_main (Thumb, 0 bytes, Stack size unknown bytes, __rtentry2.o(.ARM.Collect$$rtentry$$0000000D))

[Stack]

- Max Depth = 136 + Unknown Stack Size
- Call Chain = __rt_entry_main ⇒ main ⇒ MX_TIM3_Init ⇒ HAL_TIM_MspPostInit ⇒ HAL_GPIO_Init

[Calls]

- >> main
- >> exit

__rt_entry_postli_1 (Thumb, 0 bytes, Stack size unknown bytes, __rtentry2.o(.ARM.Collect$$rtentry$$0000000C))

__rt_exit (Thumb, 0 bytes, Stack size unknown bytes, rtexit.o(.ARM.Collect$$rtexit$$00000000))

[Called By]

- >> exit

__rt_exit_ls (Thumb, 0 bytes, Stack size unknown bytes, rtexit2.o(.ARM.Collect$$rtexit$$00000003))

[Calls]

- >> __rt_lib_shutdown

__rt_exit_prels_1 (Thumb, 0 bytes, Stack size unknown bytes, rtexit2.o(.ARM.Collect$$rtexit$$00000002))

__rt_exit_exit (Thumb, 0 bytes, Stack size unknown bytes, rtexit2.o(.ARM.Collect$$rtexit$$00000004))

[Calls]

- >> _sys_exit

Reset_Handler (Thumb, 8 bytes, Stack size 0 bytes, startup_stm32f103xe.o(.text))
[Address Reference Count : 1]

- startup_stm32f103xe.o(RESET)

ADC1_2_IRQHandler (Thumb, 0 bytes, Stack size 0 bytes, startup_stm32f103xe.o(.text))

[Calls]

- >> ADC1_2_IRQHandler

[Called By]

- >> ADC1_2_IRQHandler

[Address Reference Count : 1]

- startup_stm32f103xe.o(RESET)

ADC3_IRQHandler (Thumb, 0 bytes, Stack size 0 bytes, startup_stm32f103xe.o(.text))
[Address Reference Count : 1]

- startup_stm32f103xe.o(RESET)

CAN1_RX1_IRQHandler (Thumb, 0 bytes, Stack size 0 bytes, startup_stm32f103xe.o(.text))
[Address Reference Count : 1]

- startup_stm32f103xe.o(RESET)

CAN1_SCE_IRQHandler (Thumb, 0 bytes, Stack size 0 bytes, startup_stm32f103xe.o(.text))
[Address Reference Count : 1]

- startup_stm32f103xe.o(RESET)

DMA1_Channel1_IRQHandler (Thumb, 0 bytes, Stack size 0 bytes, startup_stm32f103xe.o(.text))
[Address Reference Count : 1]

- startup_stm32f103xe.o(RESET)

DMA1_Channel2_IRQHandler (Thumb, 0 bytes, Stack size 0 bytes, startup_stm32f103xe.o(.text))
[Address Reference Count : 1]

- startup_stm32f103xe.o(RESET)

DMA1_Channel3_IRQHandler (Thumb, 0 bytes, Stack size 0 bytes, startup_stm32f103xe.o(.text))
[Address Reference Count : 1]

- startup_stm32f103xe.o(RESET)

DMA1_Channel4_IRQHandler (Thumb, 0 bytes, Stack size 0 bytes, startup_stm32f103xe.o(.text))
[Address Reference Count : 1]

- startup_stm32f103xe.o(RESET)

DMA1_Channel5_IRQHandler (Thumb, 0 bytes, Stack size 0 bytes, startup_stm32f103xe.o(.text))
[Address Reference Count : 1]

- startup_stm32f103xe.o(RESET)

DMA1_Channel6_IRQHandler (Thumb, 0 bytes, Stack size 0 bytes, startup_stm32f103xe.o(.text))
[Address Reference Count : 1]

- startup_stm32f103xe.o(RESET)

DMA1_Channel7_IRQHandler (Thumb, 0 bytes, Stack size 0 bytes, startup_stm32f103xe.o(.text))
[Address Reference Count : 1]

- startup_stm32f103xe.o(RESET)

DMA2_Channel1_IRQHandler (Thumb, 0 bytes, Stack size 0 bytes, startup_stm32f103xe.o(.text))
[Address Reference Count : 1]

- startup_stm32f103xe.o(RESET)

DMA2_Channel2_IRQHandler (Thumb, 0 bytes, Stack size 0 bytes, startup_stm32f103xe.o(.text))
[Address Reference Count : 1]

- startup_stm32f103xe.o(RESET)

DMA2_Channel3_IRQHandler (Thumb, 0 bytes, Stack size 0 bytes, startup_stm32f103xe.o(.text))
[Address Reference Count : 1]

- startup_stm32f103xe.o(RESET)

DMA2_Channel4_5_IRQHandler (Thumb, 0 bytes, Stack size 0 bytes, startup_stm32f103xe.o(.text))
[Address Reference Count : 1]

- startup_stm32f103xe.o(RESET)

EXTI0_IRQHandler (Thumb, 0 bytes, Stack size 0 bytes, startup_stm32f103xe.o(.text))
[Address Reference Count : 1]

- startup_stm32f103xe.o(RESET)

EXTI15_10_IRQHandler (Thumb, 0 bytes, Stack size 0 bytes, startup_stm32f103xe.o(.text))
[Address Reference Count : 1]

- startup_stm32f103xe.o(RESET)

EXTI1_IRQHandler (Thumb, 0 bytes, Stack size 0 bytes, startup_stm32f103xe.o(.text))
[Address Reference Count : 1]

- startup_stm32f103xe.o(RESET)

EXTI2_IRQHandler (Thumb, 0 bytes, Stack size 0 bytes, startup_stm32f103xe.o(.text))
[Address Reference Count : 1]

- startup_stm32f103xe.o(RESET)

EXTI3_IRQHandler (Thumb, 0 bytes, Stack size 0 bytes, startup_stm32f103xe.o(.text))
[Address Reference Count : 1]

- startup_stm32f103xe.o(RESET)

EXTI4_IRQHandler (Thumb, 0 bytes, Stack size 0 bytes, startup_stm32f103xe.o(.text))
[Address Reference Count : 1]

- startup_stm32f103xe.o(RESET)

EXTI9_5_IRQHandler (Thumb, 0 bytes, Stack size 0 bytes, startup_stm32f103xe.o(.text))
[Address Reference Count : 1]

- startup_stm32f103xe.o(RESET)

FLASH_IRQHandler (Thumb, 0 bytes, Stack size 0 bytes, startup_stm32f103xe.o(.text))
[Address Reference Count : 1]

- startup_stm32f103xe.o(RESET)

FSMC_IRQHandler (Thumb, 0 bytes, Stack size 0 bytes, startup_stm32f103xe.o(.text))
[Address Reference Count : 1]

- startup_stm32f103xe.o(RESET)

I2C1_ER_IRQHandler (Thumb, 0 bytes, Stack size 0 bytes, startup_stm32f103xe.o(.text))
[Address Reference Count : 1]

- startup_stm32f103xe.o(RESET)

I2C1_EV_IRQHandler (Thumb, 0 bytes, Stack size 0 bytes, startup_stm32f103xe.o(.text))
[Address Reference Count : 1]

- startup_stm32f103xe.o(RESET)

I2C2_ER_IRQHandler (Thumb, 0 bytes, Stack size 0 bytes, startup_stm32f103xe.o(.text))
[Address Reference Count : 1]

- startup_stm32f103xe.o(RESET)

I2C2_EV_IRQHandler (Thumb, 0 bytes, Stack size 0 bytes, startup_stm32f103xe.o(.text))
[Address Reference Count : 1]

- startup_stm32f103xe.o(RESET)

PVD_IRQHandler (Thumb, 0 bytes, Stack size 0 bytes, startup_stm32f103xe.o(.text))
[Address Reference Count : 1]

- startup_stm32f103xe.o(RESET)

RCC_IRQHandler (Thumb, 0 bytes, Stack size 0 bytes, startup_stm32f103xe.o(.text))
[Address Reference Count : 1]

- startup_stm32f103xe.o(RESET)

RTC_Alarm_IRQHandler (Thumb, 0 bytes, Stack size 0 bytes, startup_stm32f103xe.o(.text))
[Address Reference Count : 1]

- startup_stm32f103xe.o(RESET)

RTC_IRQHandler (Thumb, 0 bytes, Stack size 0 bytes, startup_stm32f103xe.o(.text))
[Address Reference Count : 1]

- startup_stm32f103xe.o(RESET)

SDIO_IRQHandler (Thumb, 0 bytes, Stack size 0 bytes, startup_stm32f103xe.o(.text))
[Address Reference Count : 1]

- startup_stm32f103xe.o(RESET)

SPI1_IRQHandler (Thumb, 0 bytes, Stack size 0 bytes, startup_stm32f103xe.o(.text))
[Address Reference Count : 1]

- startup_stm32f103xe.o(RESET)

SPI2_IRQHandler (Thumb, 0 bytes, Stack size 0 bytes, startup_stm32f103xe.o(.text))
[Address Reference Count : 1]

- startup_stm32f103xe.o(RESET)

SPI3_IRQHandler (Thumb, 0 bytes, Stack size 0 bytes, startup_stm32f103xe.o(.text))
[Address Reference Count : 1]

- startup_stm32f103xe.o(RESET)

TAMPER_IRQHandler (Thumb, 0 bytes, Stack size 0 bytes, startup_stm32f103xe.o(.text))
[Address Reference Count : 1]

- startup_stm32f103xe.o(RESET)

TIM1_BRK_IRQHandler (Thumb, 0 bytes, Stack size 0 bytes, startup_stm32f103xe.o(.text))
[Address Reference Count : 1]

- startup_stm32f103xe.o(RESET)

TIM1_CC_IRQHandler (Thumb, 0 bytes, Stack size 0 bytes, startup_stm32f103xe.o(.text))
[Address Reference Count : 1]

- startup_stm32f103xe.o(RESET)

TIM1_TRG_COM_IRQHandler (Thumb, 0 bytes, Stack size 0 bytes, startup_stm32f103xe.o(.text))
[Address Reference Count : 1]

- startup_stm32f103xe.o(RESET)

TIM1_UP_IRQHandler (Thumb, 0 bytes, Stack size 0 bytes, startup_stm32f103xe.o(.text))
[Address Reference Count : 1]

- startup_stm32f103xe.o(RESET)

TIM2_IRQHandler (Thumb, 0 bytes, Stack size 0 bytes, startup_stm32f103xe.o(.text))
[Address Reference Count : 1]

- startup_stm32f103xe.o(RESET)

TIM3_IRQHandler (Thumb, 0 bytes, Stack size 0 bytes, startup_stm32f103xe.o(.text))
[Address Reference Count : 1]

- startup_stm32f103xe.o(RESET)

TIM4_IRQHandler (Thumb, 0 bytes, Stack size 0 bytes, startup_stm32f103xe.o(.text))
[Address Reference Count : 1]

- startup_stm32f103xe.o(RESET)

TIM5_IRQHandler (Thumb, 0 bytes, Stack size 0 bytes, startup_stm32f103xe.o(.text))
[Address Reference Count : 1]

- startup_stm32f103xe.o(RESET)

TIM6_IRQHandler (Thumb, 0 bytes, Stack size 0 bytes, startup_stm32f103xe.o(.text))
[Address Reference Count : 1]

- startup_stm32f103xe.o(RESET)

TIM7_IRQHandler (Thumb, 0 bytes, Stack size 0 bytes, startup_stm32f103xe.o(.text))
[Address Reference Count : 1]

- startup_stm32f103xe.o(RESET)

TIM8_BRK_IRQHandler (Thumb, 0 bytes, Stack size 0 bytes, startup_stm32f103xe.o(.text))
[Address Reference Count : 1]

- startup_stm32f103xe.o(RESET)

TIM8_CC_IRQHandler (Thumb, 0 bytes, Stack size 0 bytes, startup_stm32f103xe.o(.text))
[Address Reference Count : 1]

- startup_stm32f103xe.o(RESET)

TIM8_TRG_COM_IRQHandler (Thumb, 0 bytes, Stack size 0 bytes, startup_stm32f103xe.o(.text))
[Address Reference Count : 1]

- startup_stm32f103xe.o(RESET)

TIM8_UP_IRQHandler (Thumb, 0 bytes, Stack size 0 bytes, startup_stm32f103xe.o(.text))
[Address Reference Count : 1]

- startup_stm32f103xe.o(RESET)

UART4_IRQHandler (Thumb, 0 bytes, Stack size 0 bytes, startup_stm32f103xe.o(.text))
[Address Reference Count : 1]

- startup_stm32f103xe.o(RESET)

UART5_IRQHandler (Thumb, 0 bytes, Stack size 0 bytes, startup_stm32f103xe.o(.text))
[Address Reference Count : 1]

- startup_stm32f103xe.o(RESET)

USART2_IRQHandler (Thumb, 0 bytes, Stack size 0 bytes, startup_stm32f103xe.o(.text))
[Address Reference Count : 1]

- startup_stm32f103xe.o(RESET)

USART3_IRQHandler (Thumb, 0 bytes, Stack size 0 bytes, startup_stm32f103xe.o(.text))
[Address Reference Count : 1]

- startup_stm32f103xe.o(RESET)

USBWakeUp_IRQHandler (Thumb, 0 bytes, Stack size 0 bytes, startup_stm32f103xe.o(.text))
[Address Reference Count : 1]

- startup_stm32f103xe.o(RESET)

USB_HP_CAN1_TX_IRQHandler (Thumb, 0 bytes, Stack size 0 bytes, startup_stm32f103xe.o(.text))
[Address Reference Count : 1]

- startup_stm32f103xe.o(RESET)

USB_LP_CAN1_RX0_IRQHandler (Thumb, 0 bytes, Stack size 0 bytes, startup_stm32f103xe.o(.text))
[Address Reference Count : 1]

- startup_stm32f103xe.o(RESET)

WWDG_IRQHandler (Thumb, 0 bytes, Stack size 0 bytes, startup_stm32f103xe.o(.text))
[Address Reference Count : 1]

- startup_stm32f103xe.o(RESET)

__user_initial_stackheap (Thumb, 0 bytes, Stack size unknown bytes, startup_stm32f103xe.o(.text))

[Called By]

- >> __user_setup_stackheap

__aeabi_memclr4 (Thumb, 0 bytes, Stack size 4 bytes, rt_memclr_w.o(.text))

[Stack]

- Max Depth = 4
- Call Chain = __aeabi_memclr4

[Called By]

- >> MX_TIM3_Init
- >> MX_TIM2_Init
- >> SystemClock_Config

__aeabi_memclr8 (Thumb, 0 bytes, Stack size 4 bytes, rt_memclr_w.o(.text), UNUSED)

__rt_memclr_w (Thumb, 78 bytes, Stack size 4 bytes, rt_memclr_w.o(.text), UNUSED)

_memset_w (Thumb, 0 bytes, Stack size unknown bytes, rt_memclr_w.o(.text), UNUSED)

__use_two_region_memory (Thumb, 2 bytes, Stack size 0 bytes, heapauxi.o(.text), UNUSED)

__rt_heap_escrow$2region (Thumb, 2 bytes, Stack size 0 bytes, heapauxi.o(.text), UNUSED)

__rt_heap_expand$2region (Thumb, 2 bytes, Stack size 0 bytes, heapauxi.o(.text), UNUSED)

__user_setup_stackheap (Thumb, 74 bytes, Stack size 8 bytes, sys_stackheap_outer.o(.text))

[Stack]

- Max Depth = 8 + Unknown Stack Size
- Call Chain = __user_setup_stackheap

[Calls]

- >> __user_initial_stackheap
- >> __user_perproc_libspace

[Called By]

- >> __rt_entry_sh

exit (Thumb, 18 bytes, Stack size 8 bytes, exit.o(.text))

[Stack]

- Max Depth = 8 + Unknown Stack Size
- Call Chain = exit

[Calls]

- >> __rt_exit

[Called By]

- >> __rt_entry_main

__user_libspace (Thumb, 8 bytes, Stack size 0 bytes, libspace.o(.text), UNUSED)

__user_perproc_libspace (Thumb, 0 bytes, Stack size 0 bytes, libspace.o(.text))

[Called By]

- >> __user_setup_stackheap

__user_perthread_libspace (Thumb, 0 bytes, Stack size 0 bytes, libspace.o(.text), UNUSED)

_sys_exit (Thumb, 8 bytes, Stack size 0 bytes, sys_exit.o(.text))

[Called By]

- >> __rt_exit_exit

__I$use$semihosting (Thumb, 0 bytes, Stack size 0 bytes, use_no_semi.o(.text), UNUSED)

__use_no_semihosting_swi (Thumb, 2 bytes, Stack size 0 bytes, use_no_semi.o(.text), UNUSED)

BusFault_Handler (Thumb, 2 bytes, Stack size 0 bytes, stm32f1xx_it.o(i.BusFault_Handler))

[Calls]

- >> BusFault_Handler

[Called By]

- >> BusFault_Handler

[Address Reference Count : 1]

- startup_stm32f103xe.o(RESET)

__semihosting_library_function (Thumb, 0 bytes, Stack size 0 bytes, indicate_semi.o(.text), UNUSED)

DebugMon_Handler (Thumb, 2 bytes, Stack size 0 bytes, stm32f1xx_it.o(i.DebugMon_Handler))
[Address Reference Count : 1]

- startup_stm32f103xe.o(RESET)

Error_Handler (Thumb, 4 bytes, Stack size 0 bytes, main.o(i.Error_Handler))

[Called By]

- >> MX_USART3_UART_Init
- >> MX_USART1_UART_Init
- >> MX_TIM3_Init
- >> MX_TIM2_Init

HAL_DMA_Abort (Thumb, 70 bytes, Stack size 8 bytes, stm32f1xx_hal_dma.o(i.HAL_DMA_Abort))

[Stack]

- Max Depth = 8
- Call Chain = HAL_DMA_Abort

[Called By]

- >> HAL_UART_IRQHandler

HAL_DMA_Abort_IT (Thumb, 296 bytes, Stack size 40 bytes, stm32f1xx_hal_dma.o(i.HAL_DMA_Abort_IT))

[Stack]

- Max Depth = 40
- Call Chain = HAL_DMA_Abort_IT

[Called By]

- >> HAL_UART_IRQHandler

HAL_Delay (Thumb, 32 bytes, Stack size 16 bytes, stm32f1xx_hal.o(i.HAL_Delay))

[Stack]

- Max Depth = 16
- Call Chain = HAL_Delay

[Calls]

- >> HAL_GetTick

[Called By]

- >> main

HAL_GPIO_Init (Thumb, 462 bytes, Stack size 40 bytes, stm32f1xx_hal_gpio.o(i.HAL_GPIO_Init))

[Stack]

- Max Depth = 40
- Call Chain = HAL_GPIO_Init

[Called By]

- >> HAL_UART_MspInit
- >> HAL_TIM_MspPostInit
- >> MX_SERVO_Init
- >> MX_LED_Init
- >> MX_GPIO_Init

HAL_GPIO_WritePin (Thumb, 10 bytes, Stack size 0 bytes, stm32f1xx_hal_gpio.o(i.HAL_GPIO_WritePin))

[Called By]

- >> main

HAL_GetTick (Thumb, 6 bytes, Stack size 0 bytes, stm32f1xx_hal.o(i.HAL_GetTick))

[Called By]

- >> HAL_RCC_OscConfig
- >> HAL_RCC_ClockConfig
- >> HAL_Delay

HAL_IncTick (Thumb, 12 bytes, Stack size 0 bytes, stm32f1xx_hal.o(i.HAL_IncTick))

[Called By]

- >> SysTick_Handler

HAL_Init (Thumb, 32 bytes, Stack size 8 bytes, stm32f1xx_hal.o(i.HAL_Init))

[Stack]

- Max Depth = 40
- Call Chain = HAL_Init ⇒ HAL_InitTick ⇒ HAL_NVIC_SetPriority

[Calls]

- >> HAL_MspInit
- >> HAL_InitTick
- >> HAL_NVIC_SetPriorityGrouping

[Called By]

- >> main

HAL_InitTick (Thumb, 54 bytes, Stack size 16 bytes, stm32f1xx_hal.o(i.HAL_InitTick))

[Stack]

- Max Depth = 32
- Call Chain = HAL_InitTick ⇒ HAL_NVIC_SetPriority

[Calls]

- >> HAL_NVIC_SetPriority
- >> HAL_SYSTICK_Config

[Called By]

- >> HAL_RCC_ClockConfig
- >> HAL_Init

HAL_MspInit (Thumb, 52 bytes, Stack size 8 bytes, stm32f1xx_hal_msp.o(i.HAL_MspInit))

[Stack]

- Max Depth = 8
- Call Chain = HAL_MspInit

[Called By]

- >> HAL_Init

HAL_NVIC_EnableIRQ (Thumb, 26 bytes, Stack size 0 bytes, stm32f1xx_hal_cortex.o(i.HAL_NVIC_EnableIRQ))

[Called By]

- >> HAL_UART_MspInit

HAL_NVIC_SetPriority (Thumb, 60 bytes, Stack size 16 bytes, stm32f1xx_hal_cortex.o(i.HAL_NVIC_SetPriority))

[Stack]

- Max Depth = 16
- Call Chain = HAL_NVIC_SetPriority

[Calls]

- >> __NVIC_SetPriority

[Called By]

- >> HAL_UART_MspInit
- >> HAL_InitTick

HAL_NVIC_SetPriorityGrouping (Thumb, 26 bytes, Stack size 0 bytes, stm32f1xx_hal_cortex.o(i.HAL_NVIC_SetPriorityGrouping))

[Called By]

- >> HAL_Init

HAL_RCC_ClockConfig (Thumb, 280 bytes, Stack size 32 bytes, stm32f1xx_hal_rcc.o(i.HAL_RCC_ClockConfig))

[Stack]

- Max Depth = 64
- Call Chain = HAL_RCC_ClockConfig ⇒ HAL_InitTick ⇒ HAL_NVIC_SetPriority

[Calls]

- >> HAL_RCC_GetSysClockFreq
- >> HAL_InitTick
- >> HAL_GetTick

[Called By]

- >> SystemClock_Config

HAL_RCC_GetPCLK1Freq (Thumb, 20 bytes, Stack size 0 bytes, stm32f1xx_hal_rcc.o(i.HAL_RCC_GetPCLK1Freq))

[Called By]

- >> UART_SetConfig

HAL_RCC_GetPCLK2Freq (Thumb, 20 bytes, Stack size 0 bytes, stm32f1xx_hal_rcc.o(i.HAL_RCC_GetPCLK2Freq))

[Called By]

- >> UART_SetConfig

HAL_RCC_GetSysClockFreq (Thumb, 58 bytes, Stack size 0 bytes, stm32f1xx_hal_rcc.o(i.HAL_RCC_GetSysClockFreq))

[Called By]

- >> HAL_RCC_ClockConfig

HAL_RCC_OscConfig (Thumb, 778 bytes, Stack size 40 bytes, stm32f1xx_hal_rcc.o(i.HAL_RCC_OscConfig))

[Stack]

- Max Depth = 40
- Call Chain = HAL_RCC_OscConfig

[Calls]

- >> HAL_GetTick

[Called By]

- >> SystemClock_Config

HAL_SYSTICK_Config (Thumb, 40 bytes, Stack size 8 bytes, stm32f1xx_hal_cortex.o(i.HAL_SYSTICK_Config))

[Stack]

- Max Depth = 8
- Call Chain = HAL_SYSTICK_Config

[Calls]

- >> __NVIC_SetPriority

[Called By]

- >> HAL_InitTick

HAL_TIMEx_MasterConfigSynchronization (Thumb, 104 bytes, Stack size 16 bytes, stm32f1xx_hal_tim_ex.o(i.HAL_TIMEx_MasterConfigSynchronization))

[Stack]

- Max Depth = 16
- Call Chain = HAL_TIMEx_MasterConfigSynchronization

[Called By]

- >> MX_TIM3_Init
- >> MX_TIM2_Init

HAL_TIM_Base_Init (Thumb, 90 bytes, Stack size 8 bytes, stm32f1xx_hal_tim.o(i.HAL_TIM_Base_Init))

[Stack]

- Max Depth = 28
- Call Chain = HAL_TIM_Base_Init ⇒ TIM_Base_SetConfig

[Calls]

- >> HAL_TIM_Base_MspInit
- >> TIM_Base_SetConfig

[Called By]

- >> MX_TIM3_Init
- >> MX_TIM2_Init

HAL_TIM_Base_MspInit (Thumb, 52 bytes, Stack size 8 bytes, tim.o(i.HAL_TIM_Base_MspInit))

[Stack]

- Max Depth = 8
- Call Chain = HAL_TIM_Base_MspInit

[Called By]

- >> HAL_TIM_Base_Init

HAL_TIM_ConfigClockSource (Thumb, 220 bytes, Stack size 16 bytes, stm32f1xx_hal_tim.o(i.HAL_TIM_ConfigClockSource))

[Stack]

- Max Depth = 24
- Call Chain = HAL_TIM_ConfigClockSource ⇒ TIM_TI2_ConfigInputStage

[Calls]

- >> TIM_TI2_ConfigInputStage
- >> TIM_TI1_ConfigInputStage
- >> TIM_ITRx_SetConfig
- >> TIM_ETR_SetConfig

[Called By]

- >> MX_TIM3_Init
- >> MX_TIM2_Init

HAL_TIM_MspPostInit (Thumb, 128 bytes, Stack size 32 bytes, tim.o(i.HAL_TIM_MspPostInit))

[Stack]

- Max Depth = 72
- Call Chain = HAL_TIM_MspPostInit ⇒ HAL_GPIO_Init

[Calls]

- >> HAL_GPIO_Init

[Called By]

- >> MX_TIM3_Init
- >> MX_TIM2_Init

HAL_TIM_OC_Init (Thumb, 90 bytes, Stack size 8 bytes, stm32f1xx_hal_tim.o(i.HAL_TIM_OC_Init))

[Stack]

- Max Depth = 28
- Call Chain = HAL_TIM_OC_Init ⇒ TIM_Base_SetConfig

[Calls]

- >> HAL_TIM_OC_MspInit
- >> TIM_Base_SetConfig

[Called By]

- >> MX_TIM3_Init
- >> MX_TIM2_Init

HAL_TIM_OC_MspInit (Thumb, 2 bytes, Stack size 0 bytes, stm32f1xx_hal_tim.o(i.HAL_TIM_OC_MspInit))

[Called By]

- >> HAL_TIM_OC_Init

HAL_TIM_PWM_ConfigChannel (Thumb, 204 bytes, Stack size 16 bytes, stm32f1xx_hal_tim.o(i.HAL_TIM_PWM_ConfigChannel))

[Stack]

- Max Depth = 36
- Call Chain = HAL_TIM_PWM_ConfigChannel ⇒ TIM_OC3_SetConfig

[Calls]

- >> TIM_OC4_SetConfig
- >> TIM_OC3_SetConfig
- >> TIM_OC1_SetConfig
- >> TIM_OC2_SetConfig

[Called By]

- >> MX_TIM3_Init
- >> MX_TIM2_Init

HAL_TIM_PWM_Init (Thumb, 90 bytes, Stack size 8 bytes, stm32f1xx_hal_tim.o(i.HAL_TIM_PWM_Init))

[Stack]

- Max Depth = 28
- Call Chain = HAL_TIM_PWM_Init ⇒ TIM_Base_SetConfig

[Calls]

- >> HAL_TIM_PWM_MspInit
- >> TIM_Base_SetConfig

[Called By]

- >> MX_TIM3_Init
- >> MX_TIM2_Init

HAL_TIM_PWM_MspInit (Thumb, 2 bytes, Stack size 0 bytes, stm32f1xx_hal_tim.o(i.HAL_TIM_PWM_MspInit))

[Called By]

- >> HAL_TIM_PWM_Init

HAL_TIM_PWM_Start (Thumb, 160 bytes, Stack size 8 bytes, stm32f1xx_hal_tim.o(i.HAL_TIM_PWM_Start))

[Stack]

- Max Depth = 16
- Call Chain = HAL_TIM_PWM_Start ⇒ TIM_CCxChannelCmd

[Calls]

- >> TIM_CCxChannelCmd

[Called By]

- >> MX_SERVO_Init

HAL_UARTEx_RxEventCallback (Thumb, 2 bytes, Stack size 0 bytes, stm32f1xx_hal_uart.o(i.HAL_UARTEx_RxEventCallback))

[Called By]

- >> HAL_UART_IRQHandler
- >> UART_Receive_IT

HAL_UART_ErrorCallback (Thumb, 2 bytes, Stack size 0 bytes, stm32f1xx_hal_uart.o(i.HAL_UART_ErrorCallback))

[Called By]

- >> HAL_UART_IRQHandler
- >> UART_DMAAbortOnError

HAL_UART_IRQHandler (Thumb, 616 bytes, Stack size 24 bytes, stm32f1xx_hal_uart.o(i.HAL_UART_IRQHandler))

[Stack]

- Max Depth = 64
- Call Chain = HAL_UART_IRQHandler ⇒ HAL_DMA_Abort_IT

[Calls]

- >> HAL_DMA_Abort
- >> HAL_UART_TxCpltCallback
- >> HAL_UART_ErrorCallback
- >> HAL_UARTEx_RxEventCallback
- >> UART_Receive_IT
- >> UART_EndRxTransfer
- >> HAL_DMA_Abort_IT

[Called By]

- >> USART1_IRQHandler

HAL_UART_Init (Thumb, 100 bytes, Stack size 16 bytes, stm32f1xx_hal_uart.o(i.HAL_UART_Init))

[Stack]

- Max Depth = 96
- Call Chain = HAL_UART_Init ⇒ HAL_UART_MspInit ⇒ HAL_GPIO_Init

[Calls]

- >> HAL_UART_MspInit
- >> UART_SetConfig

[Called By]

- >> MX_USART3_UART_Init
- >> MX_USART1_UART_Init

HAL_UART_MspInit (Thumb, 186 bytes, Stack size 40 bytes, usart.o(i.HAL_UART_MspInit))

[Stack]

- Max Depth = 80
- Call Chain = HAL_UART_MspInit ⇒ HAL_GPIO_Init

[Calls]

- >> HAL_NVIC_SetPriority
- >> HAL_NVIC_EnableIRQ
- >> HAL_GPIO_Init

[Called By]

- >> HAL_UART_Init

HAL_UART_RxCpltCallback (Thumb, 2 bytes, Stack size 0 bytes, stm32f1xx_hal_uart.o(i.HAL_UART_RxCpltCallback))

[Called By]

- >> UART_Receive_IT

HAL_UART_TxCpltCallback (Thumb, 2 bytes, Stack size 0 bytes, stm32f1xx_hal_uart.o(i.HAL_UART_TxCpltCallback))

[Called By]

- >> HAL_UART_IRQHandler

HardFault_Handler (Thumb, 2 bytes, Stack size 0 bytes, stm32f1xx_it.o(i.HardFault_Handler))

[Calls]

- >> HardFault_Handler

[Called By]

- >> HardFault_Handler

[Address Reference Count : 1]

- startup_stm32f103xe.o(RESET)

MX_GPIO_Init (Thumb, 136 bytes, Stack size 40 bytes, gpio.o(i.MX_GPIO_Init))

[Stack]

- Max Depth = 80
- Call Chain = MX_GPIO_Init ⇒ HAL_GPIO_Init

[Calls]

- >> HAL_GPIO_Init

[Called By]

- >> main

MX_LED_Init (Thumb, 52 bytes, Stack size 24 bytes, led.o(i.MX_LED_Init))

[Stack]

- Max Depth = 64
- Call Chain = MX_LED_Init ⇒ HAL_GPIO_Init

[Calls]

- >> HAL_GPIO_Init

[Called By]

- >> main

MX_SERVO_Init (Thumb, 58 bytes, Stack size 24 bytes, motor.o(i.MX_SERVO_Init))

[Stack]

- Max Depth = 64
- Call Chain = MX_SERVO_Init ⇒ HAL_GPIO_Init

[Calls]

- >> HAL_TIM_PWM_Start
- >> HAL_GPIO_Init

[Called By]

- >> main

MX_TIM2_Init (Thumb, 198 bytes, Stack size 64 bytes, tim.o(i.MX_TIM2_Init))

[Stack]

- Max Depth = 136
- Call Chain = MX_TIM2_Init ⇒ HAL_TIM_MspPostInit ⇒ HAL_GPIO_Init

[Calls]

- >> HAL_TIM_PWM_Init
- >> HAL_TIM_PWM_ConfigChannel
- >> HAL_TIM_OC_Init
- >> HAL_TIM_ConfigClockSource
- >> HAL_TIM_Base_Init
- >> HAL_TIMEx_MasterConfigSynchronization
- >> HAL_TIM_MspPostInit
- >> Error_Handler
- >> __aeabi_memclr4

[Called By]

- >> main

MX_TIM3_Init (Thumb, 180 bytes, Stack size 64 bytes, tim.o(i.MX_TIM3_Init))

[Stack]

- Max Depth = 136
- Call Chain = MX_TIM3_Init ⇒ HAL_TIM_MspPostInit ⇒ HAL_GPIO_Init

[Calls]

- >> HAL_TIM_PWM_Init
- >> HAL_TIM_PWM_ConfigChannel
- >> HAL_TIM_OC_Init
- >> HAL_TIM_ConfigClockSource
- >> HAL_TIM_Base_Init
- >> HAL_TIMEx_MasterConfigSynchronization
- >> HAL_TIM_MspPostInit
- >> Error_Handler
- >> __aeabi_memclr4

[Called By]

- >> main

MX_USART1_UART_Init (Thumb, 48 bytes, Stack size 8 bytes, usart.o(i.MX_USART1_UART_Init))

[Stack]

- Max Depth = 104
- Call Chain = MX_USART1_UART_Init ⇒ HAL_UART_Init ⇒ HAL_UART_MspInit ⇒ HAL_GPIO_Init

[Calls]

- >> HAL_UART_Init
- >> Error_Handler

[Called By]

- >> main

MX_USART3_UART_Init (Thumb, 48 bytes, Stack size 8 bytes, usart.o(i.MX_USART3_UART_Init))

[Stack]

- Max Depth = 104
- Call Chain = MX_USART3_UART_Init ⇒ HAL_UART_Init ⇒ HAL_UART_MspInit ⇒ HAL_GPIO_Init

[Calls]

- >> HAL_UART_Init
- >> Error_Handler

[Called By]

- >> main

MemManage_Handler (Thumb, 2 bytes, Stack size 0 bytes, stm32f1xx_it.o(i.MemManage_Handler))

[Calls]

- >> MemManage_Handler

[Called By]

- >> MemManage_Handler

[Address Reference Count : 1]

- startup_stm32f103xe.o(RESET)

NMI_Handler (Thumb, 2 bytes, Stack size 0 bytes, stm32f1xx_it.o(i.NMI_Handler))

[Calls]

- >> NMI_Handler

[Called By]

- >> NMI_Handler

[Address Reference Count : 1]

- startup_stm32f103xe.o(RESET)

PendSV_Handler (Thumb, 2 bytes, Stack size 0 bytes, stm32f1xx_it.o(i.PendSV_Handler))
[Address Reference Count : 1]

- startup_stm32f103xe.o(RESET)

SVC_Handler (Thumb, 2 bytes, Stack size 0 bytes, stm32f1xx_it.o(i.SVC_Handler))
[Address Reference Count : 1]

- startup_stm32f103xe.o(RESET)

Servo_Control (Thumb, 42 bytes, Stack size 8 bytes, control.o(i.Servo_Control))

[Stack]

- Max Depth = 24
- Call Chain = Servo_Control ⇒ __aeabi_f2uiz

[Calls]

- >> __aeabi_ui2f
- >> __aeabi_f2uiz

[Called By]

- >> main

SysTick_Handler (Thumb, 4 bytes, Stack size 0 bytes, stm32f1xx_it.o(i.SysTick_Handler))

[Calls]

- >> HAL_IncTick

[Address Reference Count : 1]

- startup_stm32f103xe.o(RESET)

SystemClock_Config (Thumb, 94 bytes, Stack size 72 bytes, main.o(i.SystemClock_Config))

[Stack]

- Max Depth = 136
- Call Chain = SystemClock_Config ⇒ HAL_RCC_ClockConfig ⇒ HAL_InitTick ⇒ HAL_NVIC_SetPriority

[Calls]

- >> HAL_RCC_OscConfig
- >> HAL_RCC_ClockConfig
- >> __aeabi_memclr4

[Called By]

- >> main

SystemInit (Thumb, 2 bytes, Stack size 0 bytes, system_stm32f1xx.o(i.SystemInit))
[Address Reference Count : 1]

- startup_stm32f103xe.o(.text)

TIM_Base_SetConfig (Thumb, 120 bytes, Stack size 20 bytes, stm32f1xx_hal_tim.o(i.TIM_Base_SetConfig))

[Stack]

- Max Depth = 20
- Call Chain = TIM_Base_SetConfig

[Called By]

- >> HAL_TIM_PWM_Init
- >> HAL_TIM_OC_Init
- >> HAL_TIM_Base_Init

TIM_CCxChannelCmd (Thumb, 26 bytes, Stack size 8 bytes, stm32f1xx_hal_tim.o(i.TIM_CCxChannelCmd))

[Stack]

- Max Depth = 8
- Call Chain = TIM_CCxChannelCmd

[Called By]

- >> HAL_TIM_PWM_Start

TIM_ETR_SetConfig (Thumb, 20 bytes, Stack size 8 bytes, stm32f1xx_hal_tim.o(i.TIM_ETR_SetConfig))

[Stack]

- Max Depth = 8
- Call Chain = TIM_ETR_SetConfig

[Called By]

- >> HAL_TIM_ConfigClockSource

TIM_OC2_SetConfig (Thumb, 98 bytes, Stack size 20 bytes, stm32f1xx_hal_tim.o(i.TIM_OC2_SetConfig))

[Stack]

- Max Depth = 20
- Call Chain = TIM_OC2_SetConfig

[Called By]

- >> HAL_TIM_PWM_ConfigChannel

USART1_IRQHandler (Thumb, 6 bytes, Stack size 0 bytes, stm32f1xx_it.o(i.USART1_IRQHandler))

[Stack]

- Max Depth = 64
- Call Chain = USART1_IRQHandler ⇒ HAL_UART_IRQHandler ⇒ HAL_DMA_Abort_IT

[Calls]

- >> HAL_UART_IRQHandler

[Address Reference Count : 1]

- startup_stm32f103xe.o(RESET)

UsageFault_Handler (Thumb, 2 bytes, Stack size 0 bytes, stm32f1xx_it.o(i.UsageFault_Handler))

[Calls]

- >> UsageFault_Handler

[Called By]

- >> UsageFault_Handler

[Address Reference Count : 1]

- startup_stm32f103xe.o(RESET)

main (Thumb, 82 bytes, Stack size 0 bytes, main.o(i.main))

[Stack]

- Max Depth = 136
- Call Chain = main ⇒ MX_TIM3_Init ⇒ HAL_TIM_MspPostInit ⇒ HAL_GPIO_Init

[Calls]

- >> Servo_Control
- >> MX_USART3_UART_Init
- >> MX_USART1_UART_Init
- >> MX_TIM3_Init
- >> MX_TIM2_Init
- >> MX_SERVO_Init
- >> MX_LED_Init
- >> MX_GPIO_Init
- >> HAL_Init
- >> HAL_GPIO_WritePin
- >> HAL_Delay
- >> SystemClock_Config

[Called By]

- >> __rt_entry_main

__aeabi_f2uiz (Thumb, 0 bytes, Stack size 16 bytes, ffixu.o(x$fpl$ffixu))

[Stack]

- Max Depth = 16
- Call Chain = __aeabi_f2uiz

[Called By]

- >> Servo_Control

_ffixu (Thumb, 62 bytes, Stack size 16 bytes, ffixu.o(x$fpl$ffixu), UNUSED)

[Calls]

- >> __fpl_fnaninf

__aeabi_ui2f (Thumb, 0 bytes, Stack size 0 bytes, fflt_clz.o(x$fpl$ffltu))

[Called By]

- >> Servo_Control

_ffltu (Thumb, 38 bytes, Stack size 0 bytes, fflt_clz.o(x$fpl$ffltu), UNUSED)

__fpl_fnaninf (Thumb, 140 bytes, Stack size 8 bytes, fnaninf.o(x$fpl$fnaninf), UNUSED)

[Called By]

- >> _ffixu

### Local Symbols

TIM_ITRx_SetConfig (Thumb, 16 bytes, Stack size 0 bytes, stm32f1xx_hal_tim.o(i.TIM_ITRx_SetConfig))

[Called By]

- >> HAL_TIM_ConfigClockSource

TIM_OC1_SetConfig (Thumb, 88 bytes, Stack size 20 bytes, stm32f1xx_hal_tim.o(i.TIM_OC1_SetConfig))

[Stack]

- Max Depth = 20
- Call Chain = TIM_OC1_SetConfig

[Called By]

- >> HAL_TIM_PWM_ConfigChannel

TIM_OC3_SetConfig (Thumb, 96 bytes, Stack size 20 bytes, stm32f1xx_hal_tim.o(i.TIM_OC3_SetConfig))

[Stack]

- Max Depth = 20
- Call Chain = TIM_OC3_SetConfig

[Called By]

- >> HAL_TIM_PWM_ConfigChannel

TIM_OC4_SetConfig (Thumb, 70 bytes, Stack size 12 bytes, stm32f1xx_hal_tim.o(i.TIM_OC4_SetConfig))

[Stack]

- Max Depth = 12
- Call Chain = TIM_OC4_SetConfig

[Called By]

- >> HAL_TIM_PWM_ConfigChannel

TIM_TI1_ConfigInputStage (Thumb, 34 bytes, Stack size 8 bytes, stm32f1xx_hal_tim.o(i.TIM_TI1_ConfigInputStage))

[Stack]

- Max Depth = 8
- Call Chain = TIM_TI1_ConfigInputStage

[Called By]

- >> HAL_TIM_ConfigClockSource

TIM_TI2_ConfigInputStage (Thumb, 36 bytes, Stack size 8 bytes, stm32f1xx_hal_tim.o(i.TIM_TI2_ConfigInputStage))

[Stack]

- Max Depth = 8
- Call Chain = TIM_TI2_ConfigInputStage

[Called By]

- >> HAL_TIM_ConfigClockSource

__NVIC_SetPriority (Thumb, 32 bytes, Stack size 0 bytes, stm32f1xx_hal_cortex.o(i.__NVIC_SetPriority))

[Called By]

- >> HAL_NVIC_SetPriority
- >> HAL_SYSTICK_Config

UART_DMAAbortOnError (Thumb, 16 bytes, Stack size 8 bytes, stm32f1xx_hal_uart.o(i.UART_DMAAbortOnError))

[Stack]

- Max Depth = 8
- Call Chain = UART_DMAAbortOnError

[Calls]

- >> HAL_UART_ErrorCallback

[Address Reference Count : 1]

- stm32f1xx_hal_uart.o(i.HAL_UART_IRQHandler)

UART_EndRxTransfer (Thumb, 78 bytes, Stack size 0 bytes, stm32f1xx_hal_uart.o(i.UART_EndRxTransfer))

[Calls]

- >> UART_EndRxTransfer

[Called By]

- >> HAL_UART_IRQHandler
- >> UART_EndRxTransfer

UART_Receive_IT (Thumb, 194 bytes, Stack size 8 bytes, stm32f1xx_hal_uart.o(i.UART_Receive_IT))

[Stack]

- Max Depth = 8
- Call Chain = UART_Receive_IT

[Calls]

- >> HAL_UART_RxCpltCallback
- >> HAL_UARTEx_RxEventCallback

[Called By]

- >> HAL_UART_IRQHandler

UART_SetConfig (Thumb, 178 bytes, Stack size 16 bytes, stm32f1xx_hal_uart.o(i.UART_SetConfig))

[Stack]

- Max Depth = 16
- Call Chain = UART_SetConfig

[Calls]

- >> HAL_RCC_GetPCLK2Freq
- >> HAL_RCC_GetPCLK1Freq

[Called By]

- >> HAL_UART_Init

### Undefined Global Symbols

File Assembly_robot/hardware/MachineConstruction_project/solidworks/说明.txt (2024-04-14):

该模型免费分享，仅用于个人学习参考，请勿商用\谋利\毕业设计等

若用于3D打印该模型中仍有诸多不足，请自行修改调整并购买螺钉、轴承、垫片、42步进等

个人QQ：3155319540如需交流加好友时请备注

链接：https://pan.baidu.com/s/1-9ccCHdOyobv2QbqnW7ovg?pwd=8866 
提取码：8866

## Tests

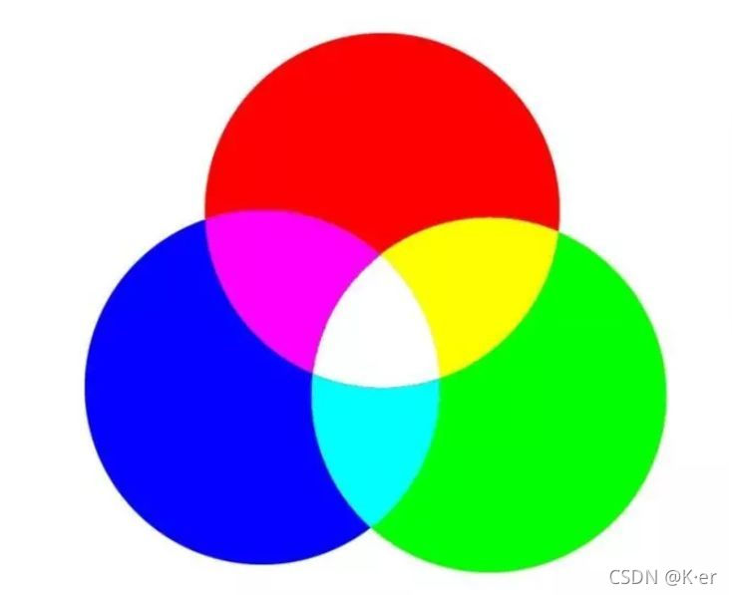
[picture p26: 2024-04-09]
Assembly_robot/software/Python_Code/test_color.jpg

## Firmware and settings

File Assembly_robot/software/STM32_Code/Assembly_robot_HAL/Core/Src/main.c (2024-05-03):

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
/* Includes ------------------------------------------------------------------*/
#include "main.h"
#include "tim.h"
#include "usart.h"
#include "gpio.h"
#include "led.h"
#include "motor.h"
#include "control.h"


/* USER CODE BEGIN PV */
/*
J1 大臂步进电机角度
J2 小臂步进电机角度
J3 底部旋转步进电机角度
J4 底部平移步进电机角度
J5 夹取舵机角度
J6 旋转舵机角度*/
uint16_t J0,J1,J2,J3,J4,J5,J6;
uint8_t RX_Data[10] = {0};
uint8_t TRANS_State;
uint16_t PLANT;
/* USER CODE END PV */

void SystemClock_Config(void);
/**
  * @brief  The application entry point.
  * @retval int
  */
int main(void)
{
  /* MCU Configuration--------------------------------------------------------*/

  /* Reset of all peripherals, Initializes the Flash interface and the Systick. */
  HAL_Init();
	
  /* USER CODE BEGIN Init */
	HAL_UART_Receive_IT(&huart1, RX_Data ,sizeof(RX_Data));
  /* USER CODE END Init */
	
  /* Configure the system clock */
  SystemClock_Config();

  /* Initialize all configured peripherals */
  MX_GPIO_Init();
  MX_TIM2_Init();
	MX_TIM3_Init();
	MX_MOTOR_Init();
  MX_USART1_UART_Init();
  MX_USART3_UART_Init();
	MX_SERVO_Init();
  /* USER CODE BEGIN 2 */
	MX_LED_Init();
  /* USER CODE END 2 */
//	MX_MOTOR_Angle(MOTOR
  /* Infinite loop */
  /* USER CODE BEGIN WHILE */
  while (1)
  {
//		HAL_GPIO_WritePin(LED_Port,LED_Pin,GPIO_PIN_SET);
		HAL_Delay(1000);	
		MOTOR1_Angle(J1);
		MOTOR2_Angle(J2);
		MOTOR3_Angle(J3);
		MOTOR4_Angle(J4);
		TRANSE_Control(TRANS_State);
		PLANT_Angle(PLANT);
		Servo1_Angle(J5);
		Servo2_Angle(J6);
		HAL_Delay(1000);
		HAL_GPIO_WritePin(LED_Port,LED_Pin,GPIO_PIN_RESET);
		HAL_Delay(1000);
    /* USER CODE END WHILE */

    /* USER CODE BEGIN 3 */
  }
  /* USER CODE END 3 */
}

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


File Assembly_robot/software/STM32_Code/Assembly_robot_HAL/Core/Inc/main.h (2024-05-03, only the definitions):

#define LSE_IN_Port GPIOC
#define LSE_IN_Pin GPIO_PIN_14
#define LSE_OUT_Port GPIOC
#define LSE_OUT_Pin GPIO_PIN_15
#define HSE_IN_Port GPIOD
#define HSE_IN_Pin GPIO_PIN_0
#define HSE_OUT_Port GPIOD
#define HSE_OUT_Pin GPIO_PIN_1
#define MOTOR1_AIN_Port GPIOC
#define MOTOR1_AIN_1_Pin GPIO_PIN_10
#define MOTOR1_AIN_2_Pin GPIO_PIN_11
#define MOTOR2_BIN_1_Port GPIOC
#define MOTOR2_BIN_1_Pin GPIO_PIN_12
#define MOTOR2_BIN_2_Port GPIOD
#define MOTOR2_BIN_2_Pin GPIO_PIN_2
#define MOTOR3_AIN_Port GPIOB
#define MOTOR3_AIN_1_Pin GPIO_PIN_5
#define MOTOR3_AIN_2_Pin GPIO_PIN_6
#define MOTOR4_BIN_Port GPIOB
#define MOTOR4_BIN_1_Pin GPIO_PIN_7
#define MOTOR4_BIN_2_Pin GPIO_PIN_4
#define USART1_Port GPIOA
#define USART1_TX_Pin GPIO_PIN_9
#define USART1_RX_Pin GPIO_PIN_10
#define USART3_Port GPIOB
#define USART3_TX_Pin GPIO_PIN_10
#define USART3_RX_Pin GPIO_PIN_11
#define TIM2_Port GPIOA 
#define TIM2_CH1_Pin GPIO_PIN_0 //大臂步进电机
#define TIM2_CH2_Pin GPIO_PIN_1 //小臂步进电机
#define TIM2_CH3_Pin GPIO_PIN_2 //底部旋转步进电机
#define TIM2_CH4_Pin GPIO_PIN_3 //直线模组步进电机
#define TIM3_CH12_Port GPIOA 
#define TIM3_CH1_Pin GPIO_PIN_6//机械爪夹取舵机
#define TIM3_CH2_Pin GPIO_PIN_7//机械爪旋转舵机
#define TRANS_Port GPIOB //传送带启停端
#define TRANS_Pin GPIO_PIN_1
#define TIM3_CH3_Port GPIOB //装配盘PUL
#define TIM3_CH3_Pin GPIO_PIN_0
#define PLANT_Port GPIOC 
#define PLANT_DIR_Pin GPIO_PIN_1 //装配盘DIR
#define PLANT_EN_Pin GPIO_PIN_2 //装配盘EN
#define LED_Port GPIOB
#define LED_Pin GPIO_PIN_13
#define LED_KEY_Pin GPIO_PIN_14
#define MOTOR_STEP_ANGLE 1.8

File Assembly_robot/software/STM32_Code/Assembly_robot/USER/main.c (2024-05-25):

#include "main.h"

uint8_t j1 = 0;
uint8_t j2 = 0;
uint8_t j3 = 90;
uint8_t j4_state = 0;
uint8_t j5 = 0; //夹取旋转舵机
uint8_t j6 = 0; //圆盘状态
uint8_t j7_state = 0;//停止
uint8_t j8_state = 0;//步进电机起始
int main(void)
{
	NVIC_PriorityGroupConfig(NVIC_PriorityGroup_2);
	delay_init();
	Motor_Init();
	Plant_Trans_Init();
	USART1_Init(115200);
	TIM1_PWM_Init(19999, 71); 
  TIM2_PWM_Init(19999, 71); 
  while(1)
	{ 
//		if(j7_state == 0)
//			TRANSE_Control(0);
//		else if(j7_state == 1)
//			TRANSE_Control(1);
		SERVO_Control1(1500);
//		MOTOR_Control(100);
		SERVO_Control2(1500);
		SERVO_Control3(0);
		SERVO_Control4(1);
		delay_ms(1000);
		SERVO_Control4(0);	
		delay_ms(1000);
		SERVO_Control5(0);
		delay_ms(1000);
	}
}

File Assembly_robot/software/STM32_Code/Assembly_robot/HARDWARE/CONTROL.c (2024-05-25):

#include "CONTROL.h"
void MOTOR_Control(uint8_t Angle)
{
	uint16_t n =(uint16_t)Angle / MOTOR_STEP_ANGLE;
	GPIO_SetBits(MOTOR_Port,MOTOR_EN);
	if(Angle > 0)
	{
		GPIO_SetBits(MOTOR_Port,MOTOR_DIR);
	}else{
		GPIO_ResetBits(MOTOR_Port,MOTOR_DIR);
	}
	for(uint16_t i =0;i<n;i++)
	{
		GPIO_SetBits(MOTOR_Port,MOTOR_PUL);
		delay_ms(1);
		GPIO_ResetBits(MOTOR_Port,MOTOR_PUL);
		delay_ms(1);
	}
}

void SERVO_Control1(uint16_t Angle) //大臂舵机
{
	uint16_t PWM = Angle;
	TIM_SetCompare1(TIM1,PWM);
}

void SERVO_Control2(uint16_t Angle) //小臂舵机
{
	uint16_t PWM = Angle;
	TIM_SetCompare4(TIM1,PWM);
}

void SERVO_Control3(uint16_t Angle) //底部旋转舵机
{
	uint16_t PWM = (Angle / 90 * 650 + 1450);
	TIM_SetCompare2(TIM2,PWM);
}

void SERVO_Control4(uint16_t state) //机械爪夹取舵机
{
	uint16_t PWM;
	if(state == 0) //闭合
		PWM = 1900;
	if(state == 1) //打开
		PWM = 1500;
	TIM_SetCompare3(TIM2,PWM);
}

void SERVO_Control5(uint16_t Angle) //机械爪旋转舵机
{
	uint16_t PWM = (Angle / 45 * 500 + 1000);
	TIM_SetCompare4(TIM2,PWM);
}

void PLANT_Control(uint8_t Angle) //圆盘角度控制
{
	GPIO_SetBits(GPIOB,PLANT_EN_Pin);
	if(Angle > 0)
	{
		uint8_t num =0;
		num = Angle/MOTOR_STEP_ANGLE;
		GPIO_SetBits(GPIOB,PLANT_DIR_Pin);
		for(int i=0;i < num;i++)
		{
			GPIO_SetBits(GPIOB,PLANT_PUL_Pin);
			delay_ms(1);
			GPIO_ResetBits(GPIOB,PLANT_PUL_Pin);
			delay_ms(1);
		}
	}else{
		GPIO_ResetBits(GPIOB,PLANT_DIR_Pin);
	}
}

void TRANSE_Control(uint8_t State)
{
	if(State == 1)
	{
		GPIO_SetBits(GPIOB,TRANS_Pin);
	}
	else if(State == 0)
	{
		GPIO_ResetBits(GPIOB,TRANS_Pin);
	}
}

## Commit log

2024-03-26 删除文件 README.md
2024-03-26 删除文件 README.en.md
2024-04-09 新增核心代码
2024-04-09 更新README
    [材料清单及引脚标号.xlsx]
2024-04-10 完善引脚定义，添加原理图
    [1_电源.schdoc.schdoc, 2_MCU.schdoc.schdoc, 3_外设.schdoc.schdoc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]
2024-04-22 更新README etc.
    [材料清单及引脚标号.xlsx]

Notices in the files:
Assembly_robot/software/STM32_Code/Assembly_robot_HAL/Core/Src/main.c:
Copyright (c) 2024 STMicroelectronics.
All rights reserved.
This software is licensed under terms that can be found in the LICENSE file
